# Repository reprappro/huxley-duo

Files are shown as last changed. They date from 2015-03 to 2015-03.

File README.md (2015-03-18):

The RepRapPro Huxley Duo 3D Printer design files repository
.
Licensed under the GPL 3, see http://www.gnu.org/copyleft/gpl.html

For more information see 

   https://reprappro.com/shop/reprap-kits/huxley-duo-kit/

STLs of the printed parts may be found in the STL directory. A full bill of materials - itemising part numbers, descriptions and required quantities - may be found in BOM.xlsx.

Hardware components that are shared with our other printers may be found in our "Library" repository

License GPL

No guarantee is made that the files contained in this project will be free
from design faults. The user accepts the risk that some issues may arise
from printing and assembling the files contained within this project. Users
are however encouraged to publish errors/improvements back to the originator.

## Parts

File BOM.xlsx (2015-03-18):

PART NUMBER | DESCRIPTION | Category | QTY.
106 | BOWDEN START |  | 2
137 | 626 BEARING |  | 2
193 | POWER JACK |  | 1
207 | LM6UU LINEAR BEARING |  | 6
219 | PTFE TUBE 4X380MM |  | 2
224 | ALUMINUM HEAT SPREADER |  | 1
235 | 6MM CLIP BUSHING |  | 4
248 | Y FROG LASER CUT 4MM MDF |  | 1
357 | HOT END HEATSINK |  | 1
455 | POWER JACK NUT |  | 1
559 | #4 SCREW |  | 6
604 | HEATBED INSULATOR |  | 1
680 | DUET ENCLOSURE BASE - HUXLEY |  | 1
736 | DUAL COLOUR COOLING BLOCK |  | 1
738 | 0.5MM STAINLESS STEEL NOZZLE |  | 2
739 | DUAL COLOUR HEATER BLOCK |  | 2
741 | LASER CUT FAN SPACER |  | 1
743 | HEATSINK SPACER |  | 1
794 | TAPERED NUT MK2 |  | 2
841 | 3MM P CLIP |  | 1
844 | HEATED BED PCB |  | 1
888 | 270mm 6mm SMOOTH ROD |  | 4
890 | 235mm x 6mm SMOOTH ROD |  | 2
891 | HOT END CONNECTOR ENCLOSURE |  | 1
130 | NEMA 14 SY35ST26 | ELECTRONICS | 4
394 | DUET | ELECTRONICS | 1
545 | PROXIMITY SENSOR PCB | ELECTRONICS | 1
597 | REGULATOR PCB | ELECTRONICS | 1
111 | M3X8 CAP HEAD | FASTENERS | 9
112 | M3X25MM CAP SCREW | FASTENERS | 5
212 | M3 PLAIN WASHER | FASTENERS | 21
242 | M3X16MM CAP SCREW | FASTENERS | 18
257 | M3X12 CAP SCREW | FASTENERS | 10
258 | M3 NUT | FASTENERS | 38
511 | M5X165MM THREADED ROD | FASTENERS | 2
520 | M3X35 CAP SCREW | FASTENERS | 9
557 | M6 BZP FULL NUT | FASTENERS | 72
558 | M6 BZP SERRATED WASHER | FASTENERS | 72
712 | M5 FULL NUT | FASTENERS | 2
818 | M3X18MM MALE/FEMALE STANDOFF VBMP-M3-5.0-18 | FASTENERS | 7
875 | M6X250MM STUDDING | FASTENERS | 6
881 | M6 X 185MM THREADED ROD | FASTENERS | 4
882 | M6 X 285MM THREADED ROD | FASTENERS | 3
918 | #4 x 1/2" BUTTON HEAD SELF TAPPING SCREW | FASTENERS | 2
185 | MICROSWITCH | HARDWARE | 1
195 | 5MM POLYTUBE | HARDWARE | 2
276 | 15X7MM SPRING | HARDWARE | 2
279 | 623 BEARING | HARDWARE | 2
577 | DUET ENCLOSURE LID | HARDWARE | 1
578 | DUET PERIMETER | HARDWARE | 1
782 | 18 TOOTH MXL PULLEY | HARDWARE | 2
846 | 40X10MM FAN | HARDWARE | 2
209 | BAR CLAMP | PRINTED PART | 4
267 | X IDLER BRACKET | PRINTED PART | 1
273 | Y BELT CLAMP | PRINTED PART | 2
316 | X MOTOR BRACKET | PRINTED PART | 1
609 | Z COUPLING | PRINTED PART | 4
610 | FRAME VERTEX WITHOUT FOOT | PRINTED PART | 2
611 | IDLER COVER | PRINTED PART | 1
614 | X CARRIAGE | PRINTED PART | 1
616 | Y BAR CLAMP | PRINTED PART | 3
618 | Y ENDSTOP HOLDER | PRINTED PART | 1
619-621 | Y IDLER BRACKET | PRINTED PART | 1
623-629 | Y MOTOR BRACKET | PRINTED PART | 1
687 | DUET BAR CLAMP | PRINTED PART | 3
714 | FAN MOUNT | PRINTED PART | 1
717 | NOZZLE MOUNT | PRINTED PART | 1
719 | Y BEARING HOLDER (FLOATING) | PRINTED PART | 1
740 | Y BELT TENSIONER | PRINTED PART | 2
742 | Y BEARING HOLDER (FIXED) | PRINTED PART | 1
169 | Z MOTOR BRACKET | PRINTED PART | 2
281 | FRAME VERTEX WITH FOOT | PRITNED PART | 4
579 | MOTOR SHIELD | SHEET METAL | 4

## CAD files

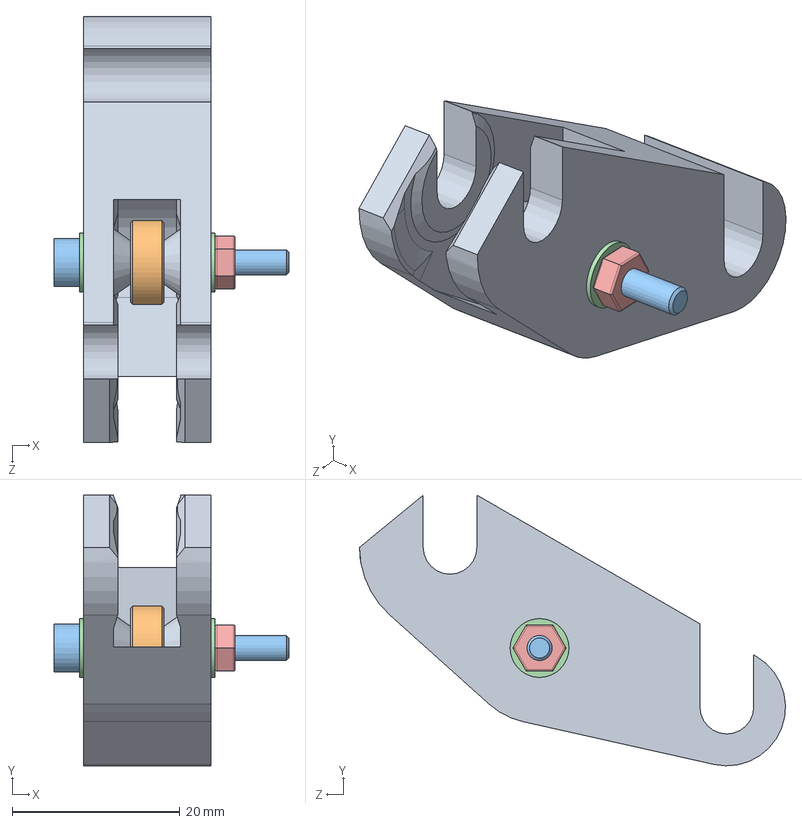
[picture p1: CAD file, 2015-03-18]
886.SLDASM
28.0 x 32.3 x 50.8 mm

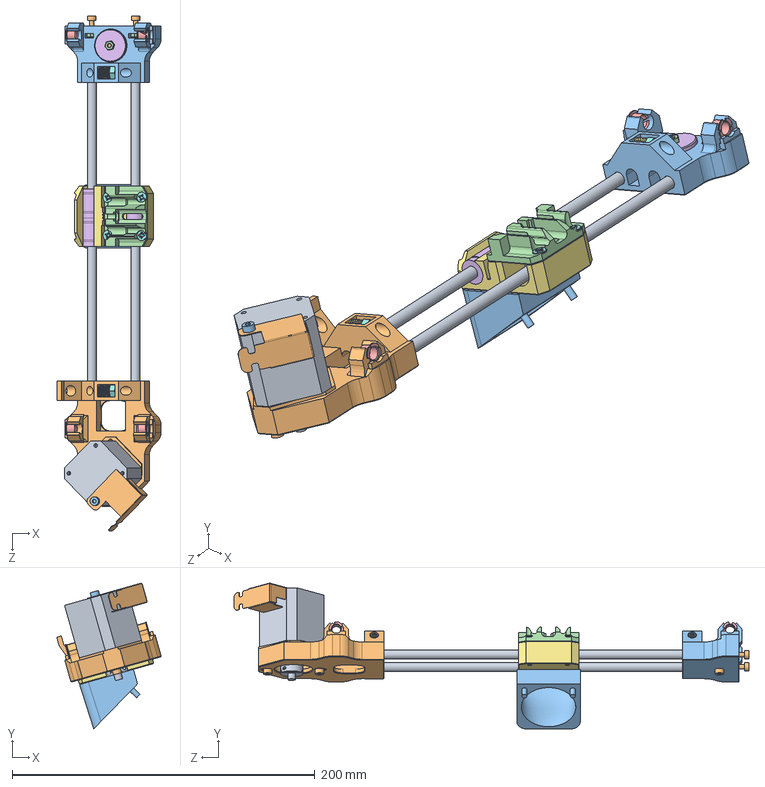
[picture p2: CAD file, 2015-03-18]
883.SLDASM
68.9 x 96.3 x 340.1 mm

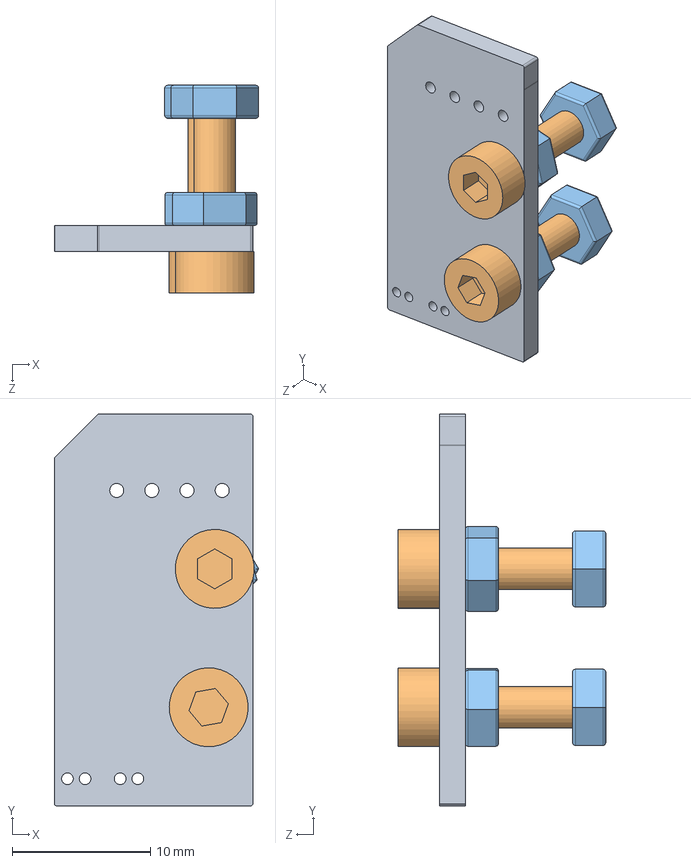
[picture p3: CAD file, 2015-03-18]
Accessories.SLDASM
14.8 x 28.3 x 15.0 mm

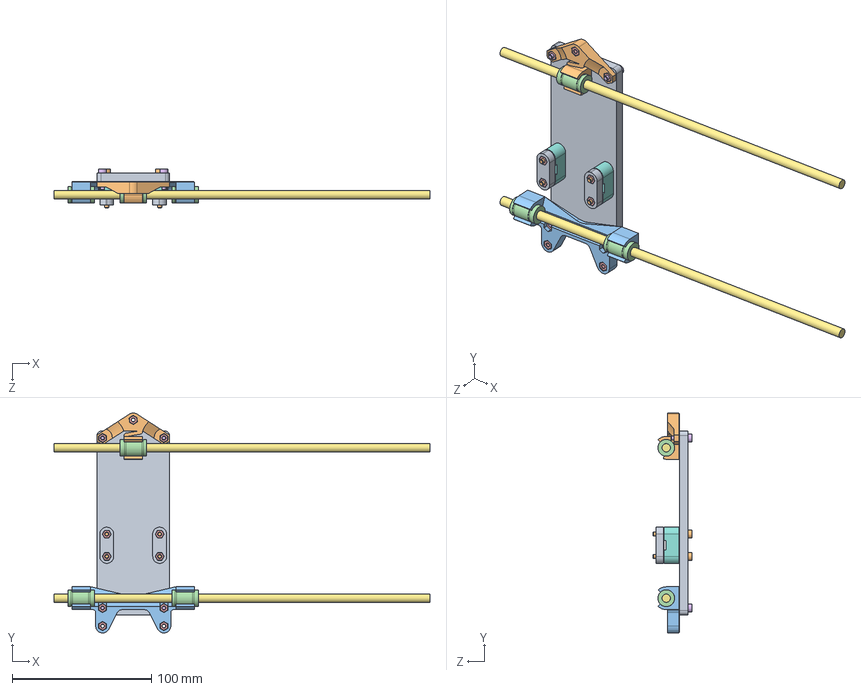
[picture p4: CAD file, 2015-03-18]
885.SLDASM
270.0 x 157.9 x 28.0 mm

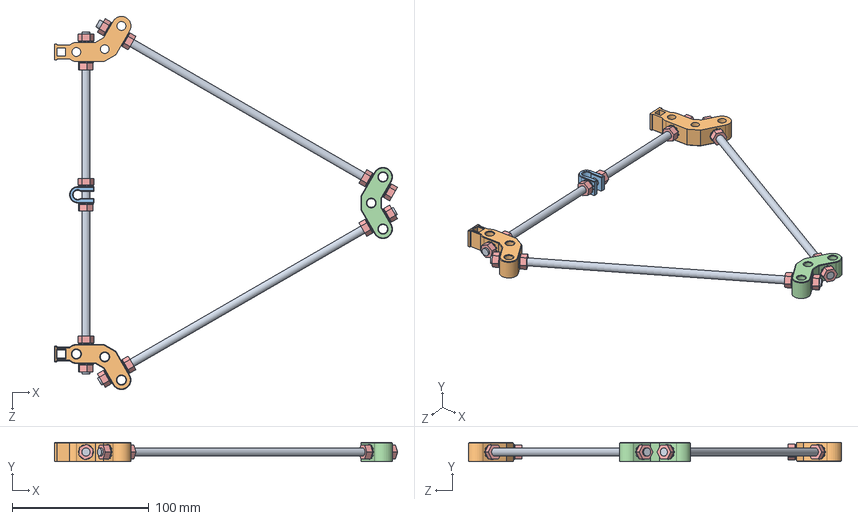
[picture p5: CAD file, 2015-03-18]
877.SLDASM
251.0 x 14.0 x 273.1 mm

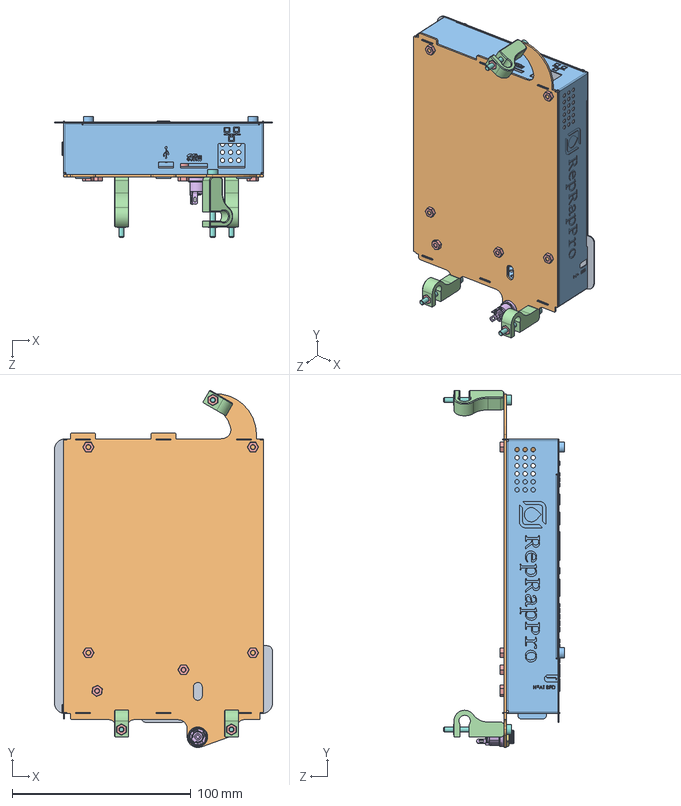
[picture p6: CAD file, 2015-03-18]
876.SLDASM
122.0 x 199.6 x 67.4 mm

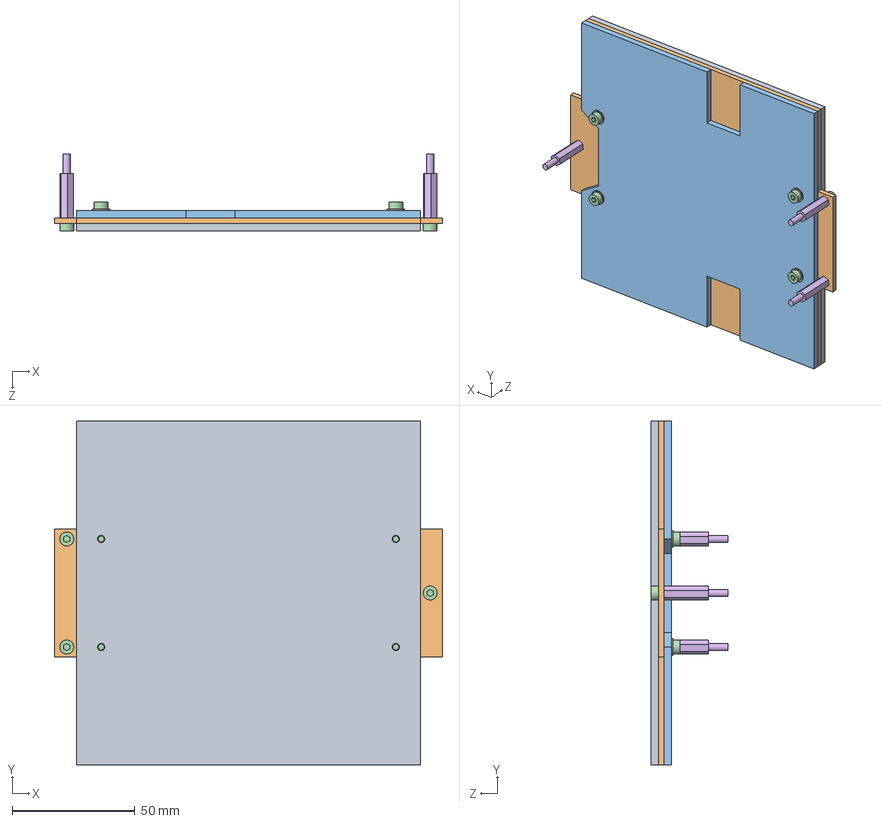
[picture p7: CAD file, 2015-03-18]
879.SLDASM
158.0 x 140.0 x 31.4 mm

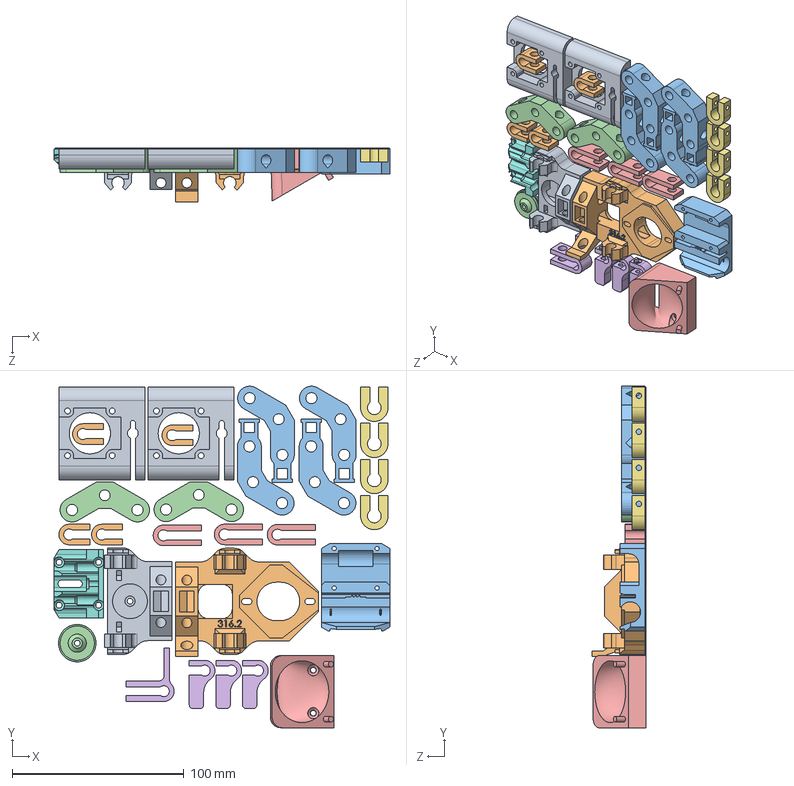
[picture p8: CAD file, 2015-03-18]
894.SLDASM
195.6 x 198.8 x 31.2 mm

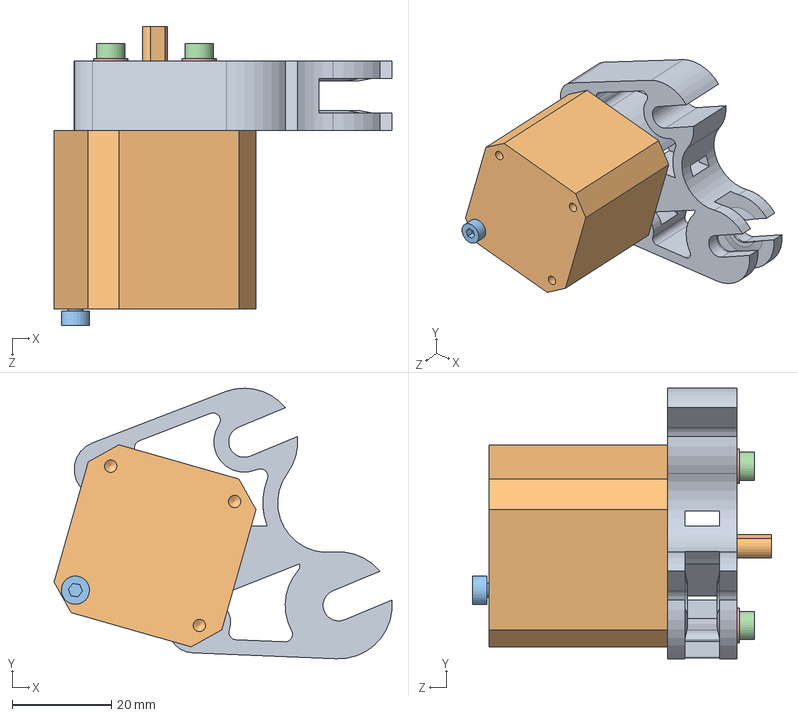
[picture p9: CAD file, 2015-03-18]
887.SLDASM
68.2 x 54.6 x 60.4 mm

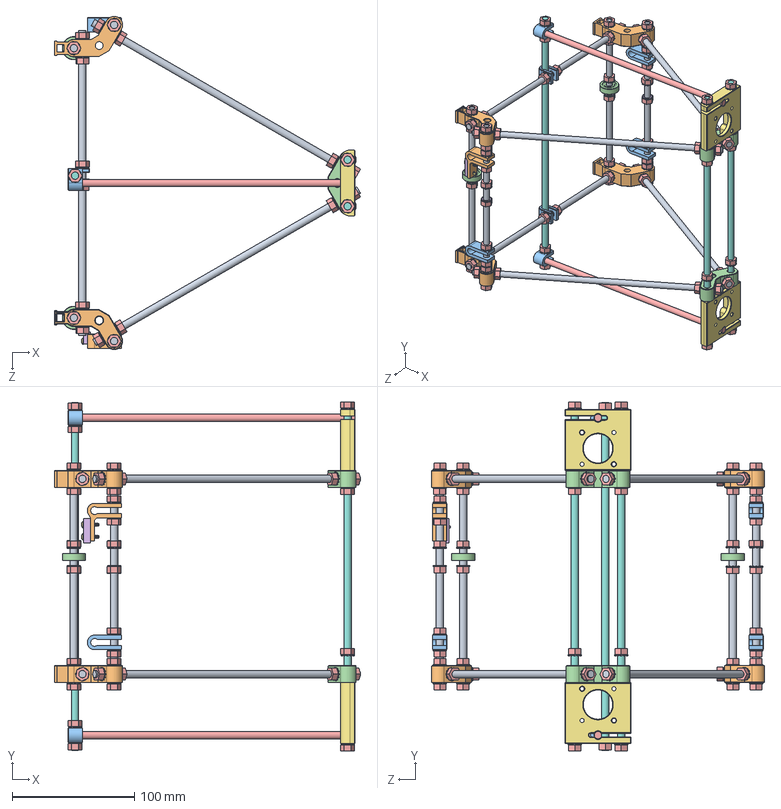
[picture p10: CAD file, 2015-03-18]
878.SLDASM
251.0 x 286.0 x 273.1 mm

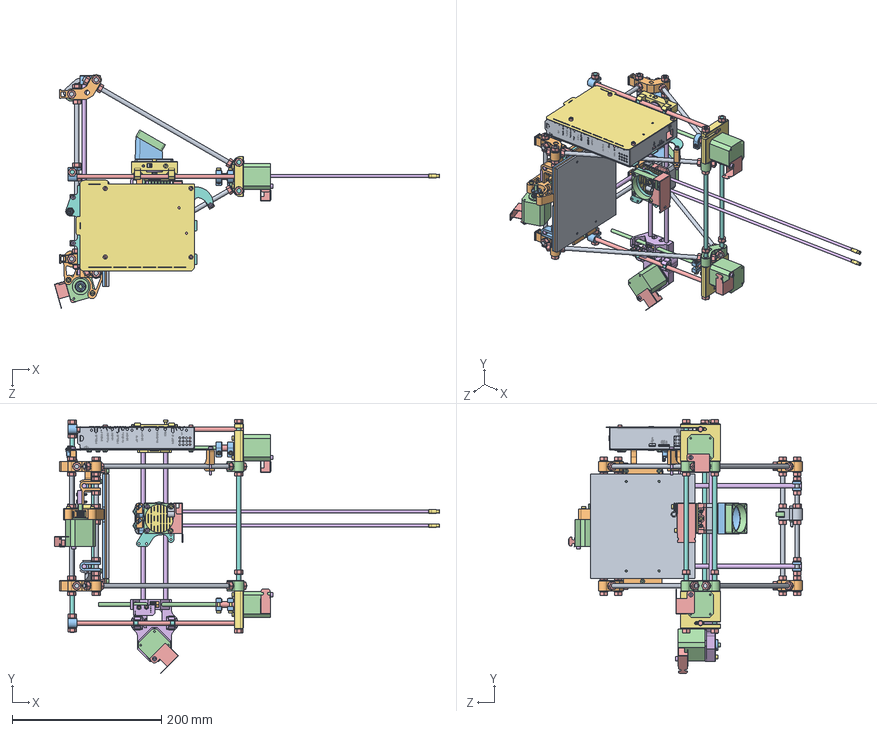
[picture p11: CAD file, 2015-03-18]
840.SLDASM
516.2 x 340.6 x 313.3 mm

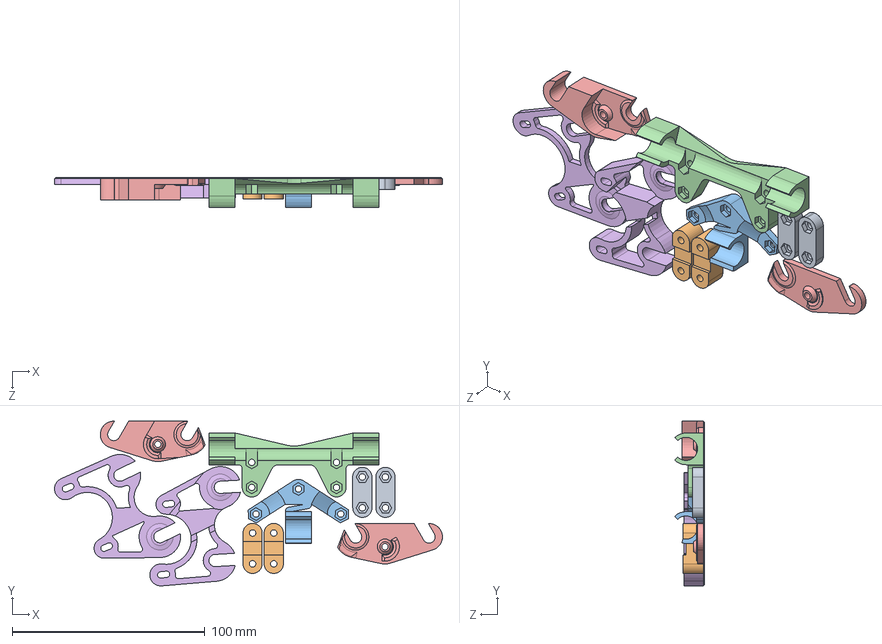
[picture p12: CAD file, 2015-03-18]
895.SLDASM
201.4 x 85.6 x 15.3 mm

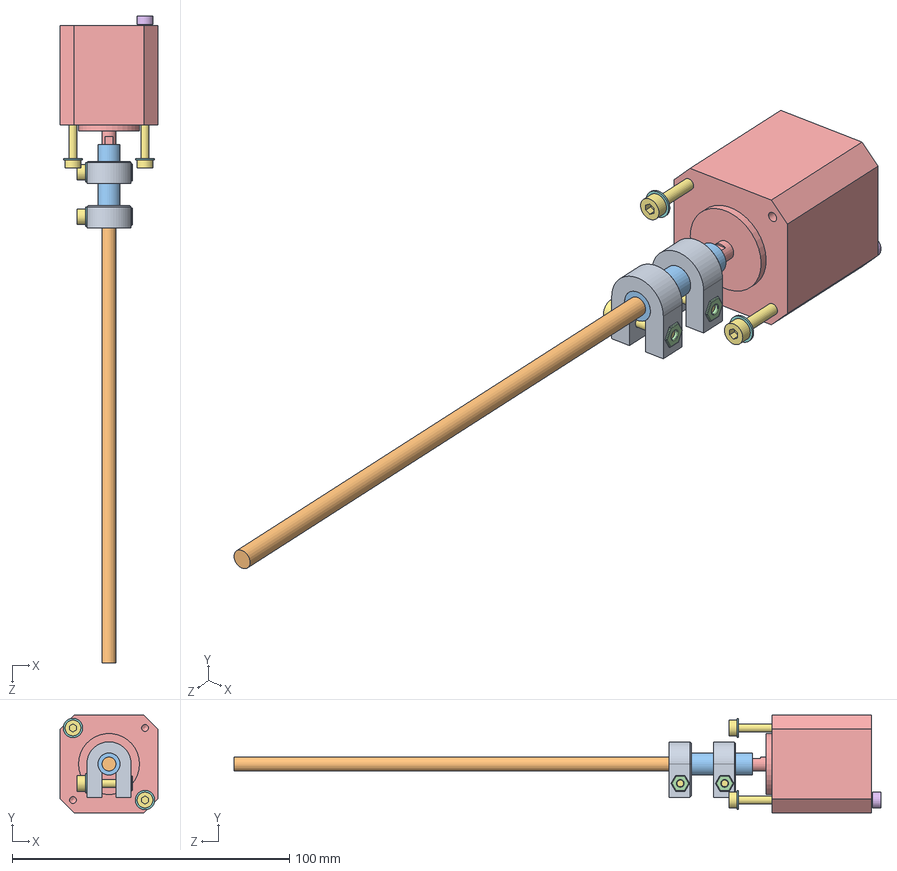
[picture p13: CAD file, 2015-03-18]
889.SLDASM
35.2 x 35.2 x 233.4 mm

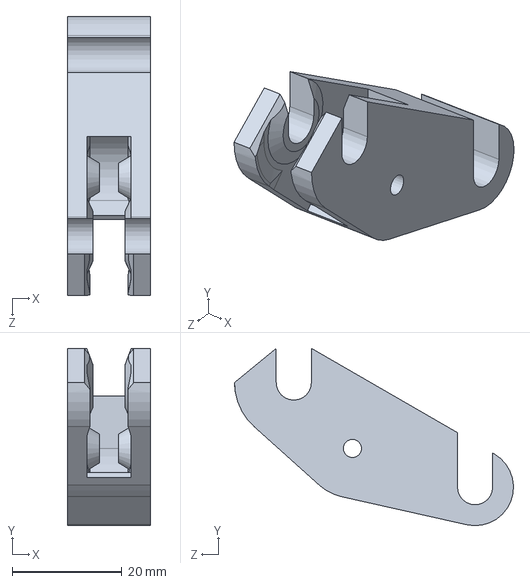
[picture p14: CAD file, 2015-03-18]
619-621.SLDPRT
15.2 x 32.3 x 50.8 mm

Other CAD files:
STLs/316-2.STL
610.SLDPRT
STLs/619.STL
616.SLDPRT
169.SLDPRT
195.SLDPRT
209.SLDPRT
224.SLDPRT
248.SLDPRT
267.SLDPRT
273.SLDPRT
281.SLDPRT
316.SLDPRT
511.SLDPRT
604.SLDPRT
611.SLDPRT
614.SLDPRT
618.SLDPRT
623-629.SLDPRT
680.SLDDRW
680.SLDPRT
687.SLDPRT
714.SLDPRT
717.SLDPRT
719.SLDPRT
740.SLDPRT
742.SLDPRT
844.SLDPRT
875.SLDPRT
881.SLDPRT
882.SLDPRT
884.SLDPRT
888.SLDPRT
890.SLDPRT
DXF/248.DXF
DXF/604.DXF
STLs/169.STL
STLs/209.STL
STLs/267.STL
STLs/273.STL
STLs/281.STL
STLs/610.STL
STLs/611.STL
STLs/614.STL
STLs/616.STL
STLs/618.STL
STLs/621.STL
STLs/623.STL
STLs/629.STL
STLs/687.STL
STLs/714.STL
STLs/717.STL
STLs/719.STL
STLs/740.STL
STLs/742.STL

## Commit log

2014-12-04 Files added.
    [169.STL, 220.STL, 267.STL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]
2015-01-05 Duet bar clamp STL file added.
    [687.STL]
2015-03-17 Bar clamp stl added
    [616.STL]
2015-03-18 Tidying and uploading SW files
    [169.SLDPRT, 169.STL, 195.SLDPRT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]
2015-05-22 Added missing stl files.
    [209.STL, 687.STL]
